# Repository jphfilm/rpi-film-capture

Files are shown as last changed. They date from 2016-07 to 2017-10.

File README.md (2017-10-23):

# rpi-film-capture

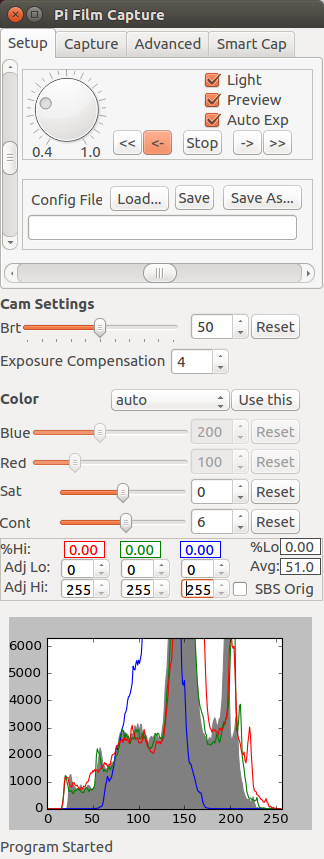
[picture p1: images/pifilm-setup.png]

A project to perform frame-by-frame capture of 8mm and 16mm films using a raspberry pi, the pi camera, and a modified movie projector. 
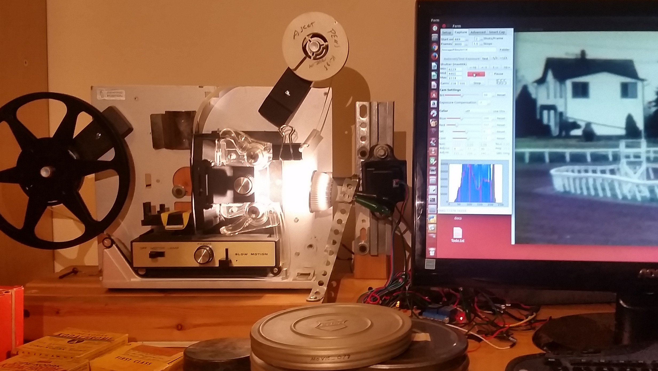
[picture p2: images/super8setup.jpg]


**UPDATE 10/23/2017: Several significant updates are coming soon, which may be worth waiting for if you're just startingout. If you're looking into this project, you may want to wait check back in a week or so, when I expect these to be available.  These include:**
* Port to Python 3 and Qt5 (currently uses python 2.7 and qt4)
* Redesigned UI to reduce need for frequent switching between panels
* Executables for linux, to avoid the complicated install/compilation process currently necessary (hopefully OSX & windows coming later)
* Flat-field correction and distortion correction to compensate for effects introduced by non-stock lenses
* Improved documentation

**Update: If you're implementing this and want suggestions/advice from other users, consider joining the [google group](https://groups.google.com/forum/#!forum/rpi-film-capture)**

Design:
* Film transport is via a repurposed projector (8mm, Super8, or 16mm), driven by a stepper motor. 
* Raspberry Pi acts as a headless server, controlling the camera, driving the motor, and streaming captured images over a network to a more powerful client.
* Python 'client' program runs on a higher-power computer on the same network. It sends control commands to the Pi server, and performs processing on images as they are captured.

Optimizations for Speed:
* Streaming images over network reduces I/O delay between frames, compared to saving them locally.
* Multithreading on both client and server further reduces I/O delays.
* All computationally demanding processing (esp. image fusion; see below) is performed by the (faster) client.
* Can capture via the Pi Camera's (slower) stills port, or can blend captures from the video port for increased speed.
* Practical per-frame capture times range from 1.6s/frame for 3-exposure bracketing from still port, down to .5s/frame for single-exposure captures from video port.

Optimizations for Quality:
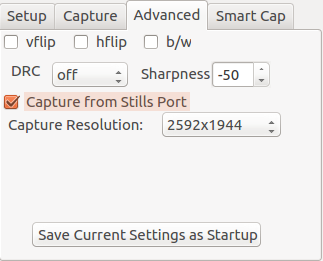
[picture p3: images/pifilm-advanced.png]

* Performs exposure bracketing on frames and combine them, to capture a much higher dynamic range than the Pi Camera normally permits.
* Full control over Pi Camera's settings, some of which may be changed mid-capture.
* Some simple histogram adjustment tools can do some processing on captured images before saving.

Optimizations for Usability:
* 'Setup Mode' allows for precise adjustment of camera before starting capture.
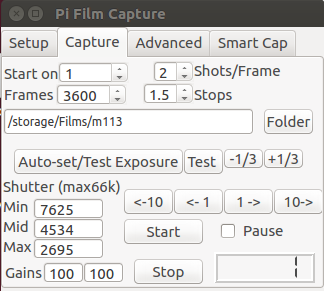
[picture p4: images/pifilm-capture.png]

* Near-real-time view of captured images.
* Save/load settings, e.g. for different film types or projector setups.
* 'Smart capture' features to adjust to dramatic lighting changes (under development)
* Entire system can be moved from one projector to another to change film gauges.

See the [wiki](https://github.com/jphfilm/rpi-film-capture/wiki)(still under construction) for complete documentation, including a manual, wiring diagrams, and hardware selection tips for your own project.

Demonstration video, samples, and comparison w/ direct capture at speed available on my [YouTube channel](https://www.youtube.com/channel/UCQi6WqZvf4OT9eOhWeVfKMg).
Many more capture examples on my [Vimeo channel](https://vimeo.com/jphfilm)

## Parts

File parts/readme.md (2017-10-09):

##3D Part Models##
Projects like this require user customization for each individual projector used, so there is no set list of parts needed.  Moreover, my part designs were amateurish 'make-do' designs which could certainly be improved upon, and I was learning openSCAD as I went, so the code could probably be better as well.

That said, I've inclded my [openSCAD](http://openscad.org) models here as a jumping-off point for other makers.  Please let me know if you improve upon these, in particular if you design a part that fits a common projector.

For those unfamiliar with openSCAD, it allows for a programmatic description of parts.  I exported these models to STL files for use with my 3d printer.

Included here are several camera mounts - some of which have several pieces - and a lamp mount.  Camera mount is without question the weakest spot of my design, and I'm actively seeking improved camera mount designs that make focus and positioning easier.

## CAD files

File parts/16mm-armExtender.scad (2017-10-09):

//My 16mm projector, an Ampro Imperial, could only accommodate 7 inch (400 foot) reels,
//but I had several larger ones. This arm extender, fitting between the projector and the 
//original arm, allows me to use 12" and larger reels on my projector.
//I drive the reel (only necessary when rewinding by combining two spring belts to create
//a larger one; the length of this belt dictates the length of the extender arm.
//I haven't changed the length of the takeup arm; I plan on cutting and resplicing the film,
//so that a larger reel will be stored on two separate 7" takeup reels

hole_diameter= 10;
hole_radius=hole_diameter/2;
arm_width=8;
arm_length=148; //hole to hole
outside_radius=8.5+hole_radius;

difference(){
union(){
translate([0,-outside_radius,0]) cube ([arm_length, outside_radius*2, arm_width]); //main arm
cylinder(h=arm_width, r=outside_radius);    //outside arm bottom
rotate([0,0,44]) cube([outside_radius,outside_radius, arm_width]); //arm stop
translate([arm_length,0,0])
    rotate([0,0,44]) 
    translate([-outside_radius,outside_radius,0])
    cube([outside_radius*2,outside_radius, arm_width]);
translate([arm_length,0,arm_width]) cylinder(h=arm_width, r=outside_radius);    //outside arm bottom
    
translate([arm_length-30,-outside_radius,arm_width]) cube([32, outside_radius*2, arm_width]);

}

cylinder(r=hole_radius, h=arm_width);
translate([arm_length,0,arm_width]) cylinder(r=hole_radius-.2, h=arm_width);
translate([arm_length,0,0]) cylinder(r=outside_radius-.3, h=arm_width);
translate([arm_length,0,0])
    rotate([0,0,44]) 
    cube([outside_radius*2,outside_radius, arm_width]);


}

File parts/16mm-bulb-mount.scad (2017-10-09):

//A mount designed to connect an MR16 led lamp to the end of the lens of my 16mm projector. 
//You will need to modify the diameters to fit your own parts.

lens_diameter=36.6;
bulb_diameter=49.5;
height=10;
coneheight=20;
insidetop=lens_diameter/2+.5;
outsidetop=lens_diameter/2+4;  
insidebottom=bulb_diameter/2+.5;
outsidebottom=bulb_diameter/2+4;
difference(){
    union(){
        translate([0,0,height+coneheight]){
            difference(){
                cylinder (h=height, r=outsidetop );
                cylinder (h=height, r=insidetop);}
            }
        translate([0,0,height]){
            difference(){
                cylinder(h=coneheight, r1=outsidebottom, r2=outsidetop);
                cylinder(h=coneheight, r1=insidebottom, r2=insidetop);}
            }
        difference(){
            cylinder (h=height, r=outsidebottom);
            cylinder (h=height, r=insidebottom);}
         }
    //Subtract cutouts from cylinders surrounding lens and bulb, to allow more 'give' when connecting mount and lamp/lens
    translate([-5,-50,0]) cube([10,100,height+1/3*coneheight]);
    translate([-50,-5,0]) cube([100,10,coneheight]);
    translate([-5,-50,height+coneheight]) cube([10,100,coneheight]);
    translate([-50,-5,height+coneheight]) cube([100,10,coneheight]);


}

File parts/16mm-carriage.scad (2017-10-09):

//A very basic mount camera mount for the 16mm projector.
//There was, luckily, a flat, horizontal section of metal casing slightly below the lens.
//The mount is primarily held to this metal with a magnet (which sits in the derpression in the base.
//I also put a bit of double-sided tape between the mount and the base, just to add a bit of tackiness so it doesn't slide around.
//I use a rubber band to secure the camera to the mount
TOTAL_WIDTH=30;
BORDER_WIDTH=3;
BORDER_HEIGHT=30;

difference() {
    cube([TOTAL_WIDTH,40,4]);       //Base of mount
    translate([15,20,1.6]) cylinder(r=9.5, h=5); //Cutout for magnet
    }

//Presumably I had something in mind when I designed this upside down and flipped it around.
//But I couldn't tell you what it was.  Sorry.
translate([TOTAL_WIDTH,0,33]){   
    rotate([180,0,-90]){
        difference(){
            //Vertical Surface for Camera Mount
            translate([-BORDER_WIDTH,0,0]){ cube([BORDER_WIDTH,TOTAL_WIDTH,BORDER_HEIGHT]);}

            //Camera Opening
            translate([-BORDER_WIDTH-1,10,8]){cube([9,9,9]);} //The hole through the mount
            translate([-BORDER_WIDTH-1,7,17]){cube([3,12,10]);} //Cutout below lens for connector between sensor chip and PCB
            translate([-BORDER_WIDTH-1,2,2]){cube([BORDER_WIDTH/2,25,25]);} //Camera Seating area
        }
    }
}

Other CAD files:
parts/8mm-base.scad
parts/8mm-cam-mount.scad
parts/8mm-carriage.scad
parts/8mm-lens-holder.scad

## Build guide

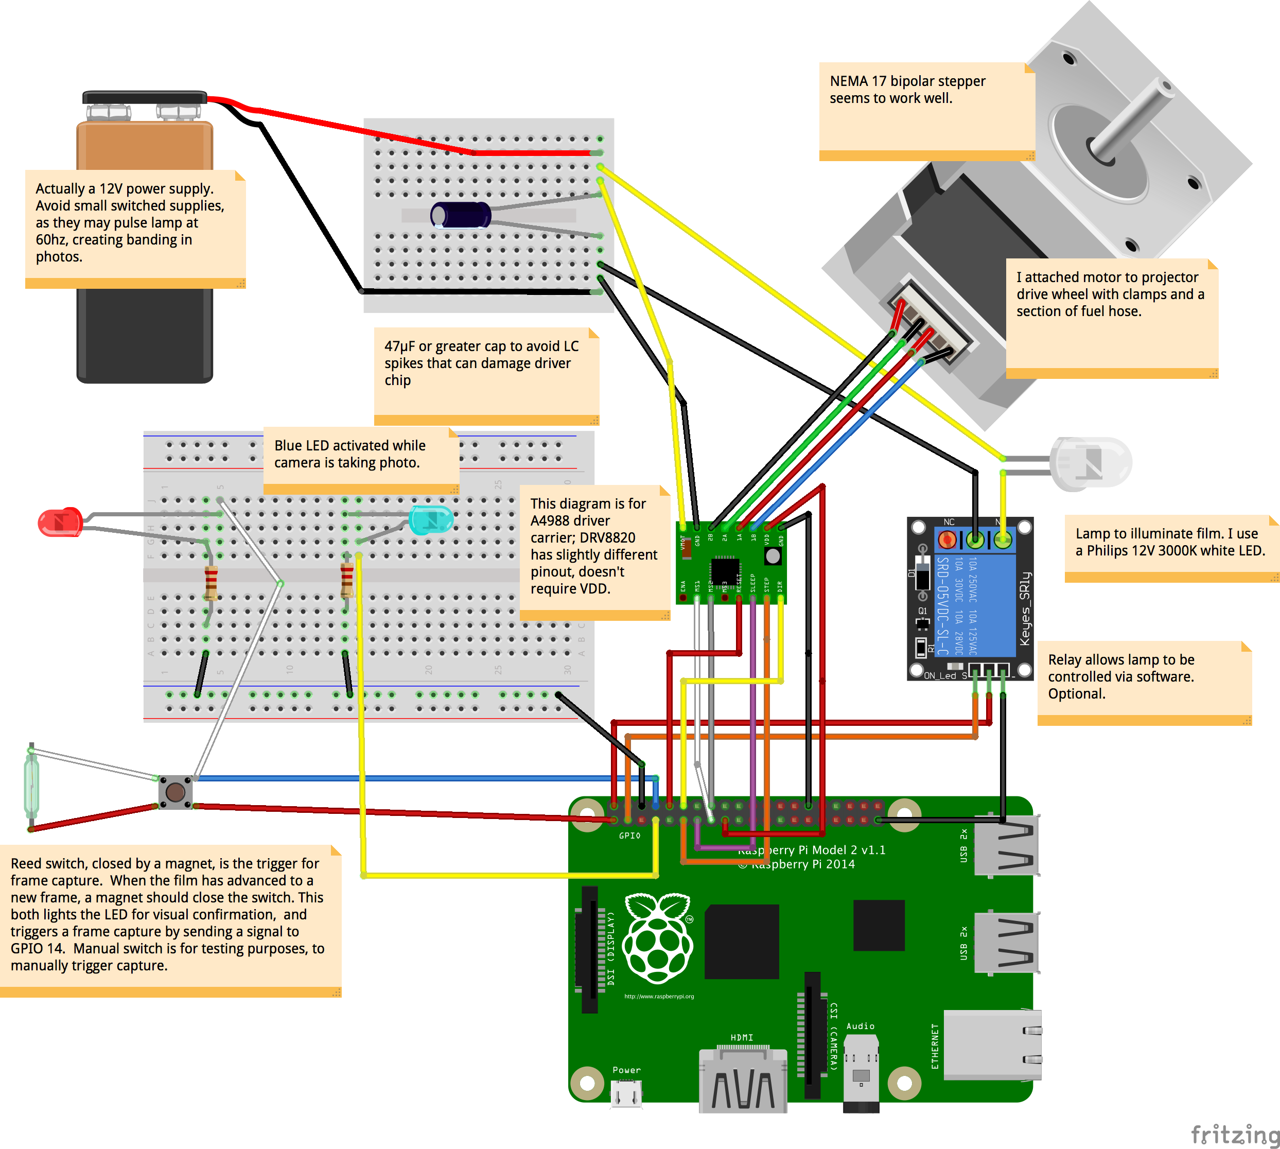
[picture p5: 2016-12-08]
images/filmcap_wiring.png

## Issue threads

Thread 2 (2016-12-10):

Link in wiki leads to blank page

brucejackson, 2016-12-10:
Hi Joe,

I found your project because of the recent article you wrote for IEEE Spectrum.  It really caught my eye as my brother and I found a bunch of family films that we would like to preserve.  I read through the wiki you provided it is informative and has inspired me to start looking at a DIY solution to preserving the movies.

On the page: https://github.com/jphfilm/rpi-film-capture/wiki/Parts-Selection, if I click on "discussion" in the "Raspberry Pi Camera and extension cable" bullet, I get an empty page at this URL (https://raw.githubusercontent.com/wiki/jphfilm/rpi-film-capture/Camera-and-Optics.md)

I was wondering if this is something you haven't written or if it is an error in the link.

Thanks for sharing all your effort and experience!
Bruce.

jphfilm, 2016-12-10:
Bruce,
It's a page I neglected to write initially; the project and wiki existed in
obscurity for a while after my initial upload so I had it on my "one of
these days I should get to that" todo list, but it's got much more traffic
since the Spectrum article appeared so I should definitely write that part
now.  I'll get something basic up there today and try to add more early
next week.
I'm delighted that people might actually be using it and trying something
like this themselves.  If you have any questions or suggestions as you work
through this stuff, please don't hesitate to contact me at
jopher91@gmail.com

On Sat, Dec 10, 2016 at 11:43 AM, Bruce Jackson <notifications@github.com>
wrote:

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

markhern, 2016-12-11:
Joe, O'Reilly Media is linking to your Spectrum article and that is how I found it. Kudos on the phenomenal work, and the results are beautiful as you described. Thank you for releasing this project to the world so that other can benefit. It's quite nice that you have a Christmas related family video as an example at this time of year. Christmas memories make these type of projects all the more important. Thanks again.

jphfilm, 2016-12-12:
@markhern, Thanks!  Could you guide me to the O'Reilly link (for ego-boosting purposes)?  I couldn't find it in a quick search.

djsinned, 2016-12-12:
Hi Joe, the link I believe is this one.
http://spectrum.ieee.org/geek-life/hands-on/how-to-convert-old-film-reels-with-a-raspberry-pi

Cheers
Dennis

jphfilm, 2016-12-12:
Oh, THAT I knew of! I thought Oreilly.com might have something, per
markhern. Thanks for replying though.

On Mon, Dec 12, 2016 at 1:54 PM, Dennis Mondolo <notifications@github.com>
wrote:

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

markhern, 2016-12-12:
Joe, the link was from the O'Reilly Programming newsletter which I signed up to receive in my email. It doesn't appear to be a regular part of the OR website. Hopefully, this link below opens for you:
http://post.oreilly.com/form/oreilly/viewhtml/9z1z2kqe0ntht906aebhpeiltadurgv9sn9l4l4p68o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

jphfilm, 2016-12-13:
Thanks! Good to know.

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

Closed 2016-12-10.

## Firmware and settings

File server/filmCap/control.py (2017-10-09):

import time
import RPi.GPIO as GPIO
from timeit import default_timer as timer
import logging
import collections
import multiprocessing

class fcControl():
    light_pin = 2
    red_pin = 3
    yellow_pin = 4
    trigger_pin = 14
    speed = 100
    frame_advance_pct=50  #This is the CUSHION - we advance 100 minus this amt after trigger
 
    
    def __init__(self):
        GPIO.setmode(GPIO.BCM)
        self.light = lightControl(self.light_pin, True)
        self.redled = lightControl(self.red_pin)
        self.yellowled = lightControl(self.yellow_pin)
        self.motor = stepperControl()
        GPIO.setup(self.trigger_pin, GPIO.IN, pull_up_down=GPIO.PUD_DOWN)
        self.motorstate = 0
        self.smart_motor = False
        self.smart_headroom = 25
        self.triggertime = 0
        self.qlen = 5
        self.triggertimes = collections.deque([],self.qlen)
        self.phototimes = collections.deque([],self.qlen)
        

    def light_on(self):
        self.light.on()
    def light_off(self):
        self.light.off()
    def red_on(self):
        self.redled.on()
    def red_off(self):
        self.redled.off()
    def yellow_on(self):
        self.yellowled.on()
    def yellow_off(self):
        self.yellowled.off()
    def yellow_is_on(self):
        return GPIO.input(self.yellow_pin)

    def cleanup(self):
        logging.info("Cleaning up GPIO")
        self.light.off()
        self.redled.off()
        self.yellowled.off()
        self.motor.stop()
        GPIO.cleanup()

    def motor_wake(self):
        self.motor.wake()
    def motor_sleep(self):
        self.motor.sleep()
        

    def motor_fwd(self, speed=False):
        if (not speed):
            speed = self.speed
        self.motor.fwd(speed)
        self.motorstate = 1
    def motor_rev(self, speed=False):
        if (not speed):
            speed = self.speed
        self.motor.rev(speed)
        self.motorstate = -1
    def motor_stop(self):
        self.motor.stop()
        self.triggertimes.clear()
        self.phototimes.clear()
        if self.motorstate:
            self.motor.center(self.trigger_pin, self.frame_advance_pct, self.motorstate)
        self.motorstate = 0
        self.motor.sleep()
    def calibrate(self):
        self.motor.center(self.trigger_pin, self.frame_advance_pct, 1)


    def end_photo(self):
        newtime = timer()
        phototime = newtime - self.triggertime
        self.phototimes.appendleft(phototime)
        
class lightControl:
    def __init__(self, pin, reversed=False):
	self.pin = pin
	self.reversed = reversed
	GPIO.setup(pin, GPIO.OUT)
	self.off()

    def on(self):
	GPIO.output( self.pin, not(self.reversed) )

    def off(self):
	GPIO.output( self.pin, self.reversed )

class stepperControl:
    pulse_freq = 1000 
    #stepper motor control pins
    dir_pin = 18
    ms1_pin = 22
    ms2_pin = 23
    sleep_pin = 27
    reset_pin = 15
    pulse_pin = 17
    half_pulse = .001 #for frame advance
    steps_per_rev = 200 #also change for MotorDriver class below
    
    def __init__(self):
        GPIO.setmode(GPIO.BCM)
        GPIO.setup(self.dir_pin, GPIO.OUT)
        GPIO.setup(self.pulse_pin, GPIO.OUT)
        GPIO.setup(self.ms1_pin, GPIO.OUT)
        GPIO.setup(self.ms2_pin, GPIO.OUT)
        GPIO.setup(self.sleep_pin, GPIO.OUT)
        GPIO.setup(self.reset_pin, GPIO.OUT)
        dir=False
        GPIO.output(self.dir_pin, dir)
        GPIO.output(self.pulse_pin, False)
        GPIO.output(self.ms1_pin, True)
        GPIO.output(self.ms2_pin, False)
        GPIO.output(self.sleep_pin, False)
        GPIO.output(self.reset_pin, True)
        self.p1 = GPIO.PWM(self.pulse_pin, self.pulse_freq)

    def wake(self):
        GPIO.output(self.sleep_pin, True)
        logging.debug("motor waking")
        time.sleep(.1)

    def sleep(self):
        GPIO.output(self.sleep_pin, False)
        logging.debug("motor sleeping")
        time.sleep(.1)

    def stop(self):
        self.p1.stop()
        GPIO.output(self.dir_pin, False)
        
    def fwd(self, speed=100):
        self.wake()
        self.p1.stop()
        time.sleep(.5)
        self.p1.ChangeFrequency(self.pulse_freq*speed/100)
        logging.debug(self.pulse_freq*speed/100)
        GPIO.output(self.dir_pin, False)
        logging.debug("motor starting fwd")        
        self.p1.start(20)
        
    def rev(self, speed=100):
        self.wake()
        self.p1.stop()
        time.sleep(.5)
        self.p1.ChangeFrequency(self.pulse_freq*speed/100)
        GPIO.output(self.dir_pin, True)
        logging.debug("motor starting rev")
        self.p1.start(20)

    def fwdFrame(self, num=1):
        self.wake()
        logging.debug("fwdFrame "+str(num))
        self.windFrame(num)
        self.sleep()

    def windFrame(self, num=1):
        pin=self.pulse_pin  #directly accessing for speed
        hp=self.half_pulse
        for i in range (0,int(self.steps_per_rev*num)):
            GPIO.output(pin, True) #used instead of variable for speed
            time.sleep(hp) #again, directly entring num for speed
            GPIO.output(pin, False) #used instead of variable for speed
            time.sleep(hp)        
 
    def revFrame(self, num=1):  #winds back one more than necessary, then forward to properly frame
        logging.debug("revFrame "+str(num))
        self.wake()
        if num==1:
            GPIO.output(self.dir_pin, True)
            self.windFrame()
            GPIO.output(self.dir_pin, False)
        else:
            GPIO.output(self.dir_pin, True)
            self.windFrame(num+1)
            GPIO.output(self.dir_pin, False)
            time.sleep(.25)
            self.windFrame(1)
        self.sleep()
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

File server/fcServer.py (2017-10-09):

#!/usr/bin/python
import socket
import time
import picamera
import threading        #should probably change threads to processes. Sometime.
import multiprocessing  #using processes instead of threads for frame advance.
import filmCap
from time import sleep
import RPi.GPIO as GPIO
from filmCap import config
from filmCap import codes

import logging
loglevel = logging.DEBUG #SET TO [CRITICAL|ERROR|WARNING|INFO|DEBUG]
logging.basicConfig(level=logging.DEBUG, format='%(asctime)s - %(levelname)s - %(message)s')

#FOR SERVER-BASED EXPOSURE CONTROL
imgbrightness = 100
imgbrightness2 = 80
brt_max_single = 150
brt_max_double = 170
brt_min_single = 70
brt_min_double = 50

calibrate_motor_every = 100
framecount = 0

missed_frames = 0
img_format = 'jpeg'  #Works with other formats, but large sizes make it much slower.
jpeg_quality = 100

auto_advance = False #this determines whether we advance after each photo
                     #turned on/off by commands from client   
readerExitEvent = threading.Event()
cap_event = multiprocessing.Event()
exit_event = multiprocessing.Event()

def setupConns(img_socket, ctrl_socket):
    global ctrl_reader, readerExitEvent
    readerExitEvent.clear()
    logging.info("Waiting for client connection...")
    config.img_conn = img_socket.accept()[0].makefile('wb')
    config.ctrl_conn = ctrl_socket.accept()[0].makefile('rb')
    logging.info("Client Connections Established")
    ctrl_reader=filmCap.NonBlockingStreamReader(config.ctrl_conn, readerExitEvent)

def releaseClient():
    global img_socket, ctrl_socket, ctrl_reader, readerExitEvent
    readerExitEvent.set()
    ctrl_reader.thr.join()
    config.img_conn.flush()
    config.img_conn.close()
    config.ctrl_conn.flush()
    config.ctrl_conn.close()
    logging.info("Client connections released")
    setupConns(img_socket, ctrl_socket) #wait for new connection from client

def sendquit():
    config.img_conn.write("t") #to tell server we're done sending
    config.img_conn.flush()

def processCmd(cmdstr):
    global fc, auto_advance
    cam=config.cam
    c=filmCap.codes
    if not cmdstr:
        logging.debug("Empty Command String")
        return 0
    cmdstr=cmdstr.replace("\n", "")
    logging.debug(cmdstr)
    cmd=cmdstr[0]
    setting=cmdstr[1:]

    #preview settings
    if cmd == c.MOTOR_FWD:
		cam.tmpmode=cam.mode
		if cam.tmpmode==cam.CAPTURING:
			cam.mode=cam.OFF
		fc.motor_fwd(50)
    elif cmd == c.MOTOR_REV:
		cam.tmpmode=cam.mode
		if cam.tmpmode==cam.CAPTURING:
			cam.mode=cam.OFF
		fc.motor_rev(50)
    elif cmd == c.MOTOR_FFD:
		cam.tmpmode=cam.mode
		if cam.tmpmode==cam.CAPTURING:
			cam.mode=cam.OFF
		fc.motor_fwd(100)
    elif cmd == c.MOTOR_FREV:
		cam.tmpmode=cam.mode
		if cam.tmpmode==cam.CAPTURING:
			cam.mode=cam.OFF
		fc.motor_rev(100)
    elif cmd == c.MOTOR_STOP:
		fc.motor_stop()
		cam.mode=cam.tmpmode


    elif cmd == c.LIGHT_OFF:
        fc.light_off()
    elif cmd == c.LIGHT_ON:
        fc.light_on()
    elif cmd == c.PREVIEW_ON:
        cam.mode = cam.PREVIEWING
    elif cmd ==  c.PREVIEW_OFF:
        cam.mode = cam.OFF
    elif cmd == c.AUTOEXP_ON:
        cam.exposure_mode = "auto"
    elif cmd ==  c.AUTOEXP_OFF:
        cam.exposure_mode = "off"
        
    elif cmd == c.SETX:
        cam.setx(int(setting))
    elif cmd == c.SETY:
        cam.sety(int(setting))
    elif cmd == c.SETZ:
        cam.setz(int(setting))
    # Color Settings
    elif cmd == c.GAIN_RED:
        cam.set_yuv(0,float(setting)/100)
    elif cmd == c.GAIN_BLUE:
        cam.set_yuv(1,float(setting)/100)
    elif cmd == c.BRIGHTNESS:
        cam.brightness = int(setting)
    elif cmd == c.EXP_COMP:
        cam.exposure_compensation = int(setting)
    elif cmd == c.SATURATION:
        cam.saturation = int(setting)
    elif cmd == c.CONTRAST:
        cam.contrast = int(setting)
    elif cmd ==  c.FIX_GAINS:
        cam.fixAndSendGains()
    elif cmd == c.AWB_MODE:
        cam.awb_mode = setting

    #Advanced controls
    elif cmd == c.DRC:
        cam.drc_strength = setting
    elif cmd == c.HFLIP_ON:
        cam.hflip = True
    elif cmd == c.HFLIP_OFF:
        cam.hflip = False
    elif cmd == c.VFLIP_ON:
        cam.vflip = True
    elif cmd == c.VFLIP_OFF:
        cam.vflip = False
    elif cmd == c.BW_ON:
        cam.color_effects = (128,128)
    elif cmd == c.BW_OFF:
        cam.color_effects = None
    elif cmd == c.SHARPNESS:
        cam.sharpness = int(setting)
    elif cmd == c.VID_PORT_ON:
        cam.vidcap = True
    elif cmd == c.VID_PORT_OFF:
        cam.vidcap = False
    elif cmd == c.SET_SIZE:
        cam.setResize(int(setting))

    #Capture settings for tab switch
    elif cmd == c.CAPTURE_ON:
        if cam.mode != cam.CAPTURING:
            fc.light_on()
            cam.startCaptureMode()
            take_a_photo(0)
    elif cmd == c.CAPTURE_OFF:
        if cam.mode == cam.CAPTURING:
            cam.startPreviewMode()

    #Capture settings
    elif cmd == c.BRACKETING_SHOTS:
        cam.bracketing=int(setting)
        cam.sendss=True
    elif cmd == c.BRACKETING_STOPS:
        cam.stops = float(setting)
        cam.sendss=True
    elif cmd == c.FIX_EXPOSURE:
        cam.setExposure()
        take_a_photo(0) #take a single photo and stream it.
    elif cmd == c.SS_SLOWER:
        cam.ss = int(cam.ss * 1.23)
        cam.shutter_speed = int(cam.ss)
        cam.sendss = True
    elif cmd == c.SS_FASTER:
        cam.ss = int(cam.ss * .81)
        cam.shutter_speed = int(cam.ss)
        cam.sendss = True
    elif cmd == c.QUIT:
        config.exitEvent.set()
    elif cmd == c.CLIENT_QUIT:
        cam.mode = cam.OFF
        sendquit()
        time.sleep(2)
        releaseClient()
    elif cmd == c.TEST_PHOTO:
        take_a_photo(0) #take a single photo and stream it.
        cam.sendss = True
    elif cmd == c.START_CAPTURE:
        auto_advance=True
        fc.motor_wake()
        take_a_photo(0)
    elif cmd == c.STOP_CAPTURE:
        auto_advance=False
        #fc.motor_sleep()
    elif cmd == c.RESUME_CAPTURE:
        global cap_event
        auto_advance=True
        fc.motor_wake()
        #Don't take a photo, b/c we should have got the last frame. Just advance a frame.
        cap_event.set()
        #fc.motor_sleep()
    elif cmd == c.CAP_FRAME_ADV:
        cam.mode=cam.OFF
        num=int(setting) if setting else 1
        fc.motor.fwdFrame(num)  
        cam.mode=cam.CAPTURING
        take_a_photo(0) #take a single photo and stream it.
    elif cmd == c.CAP_FRAME_REV:
        cam.mode=cam.OFF
        auto_advance = False
        num=int(setting) if setting else 1
        fc.motor.revFrame(num)  
        cam.mode=cam.CAPTURING
        take_a_photo(0) #take a single photo and stream it.

    #smart capture settings
    elif cmd -- '^':
        if setting:
            fc.smart_motor = True
            fc.smart_headroom = setting
        else:
            fc.smart_motor = False
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

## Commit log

2016-07-28 Fix bugs and add image post-capture historgram stretching of images
    [codes.py]
2016-07-28 Bugfixes and minor enhancements
    [camera.py, codes.py, control.py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]
2016-12-08 Modified to allow changes to preview settings (zoom/x/y) without switching to preview mode Disable capture start/stop while paused
2016-12-08 Fixed improper wiring for reed switch
2016-12-16 Add scad files for 8mm camera mount
    [8mm-base.scad, 8mm-cam-mount.scad, 8mm-carriage.scad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]
2017-10-09 Use Qt for image display, and improve single-frame capture from video port
2017-10-09 Client: Display image using Qt functions, to avoid conflicts w/ OpenCV. Server: Delay photos until after motor stops, because vibrations affect single-frame captures from video port.
    [camera.py, control.py, fcServer.py]
